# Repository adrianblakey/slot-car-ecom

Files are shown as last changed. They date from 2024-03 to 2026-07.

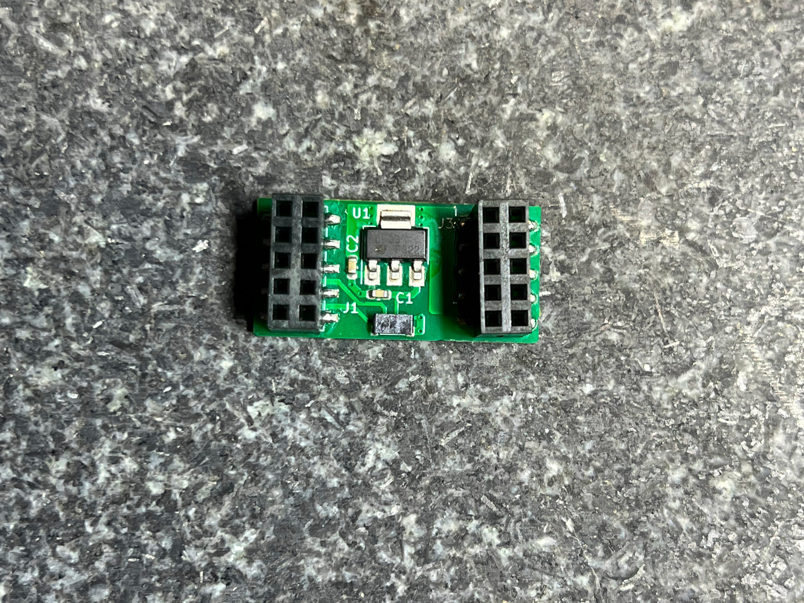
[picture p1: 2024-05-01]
images/aart-adapter.jpg

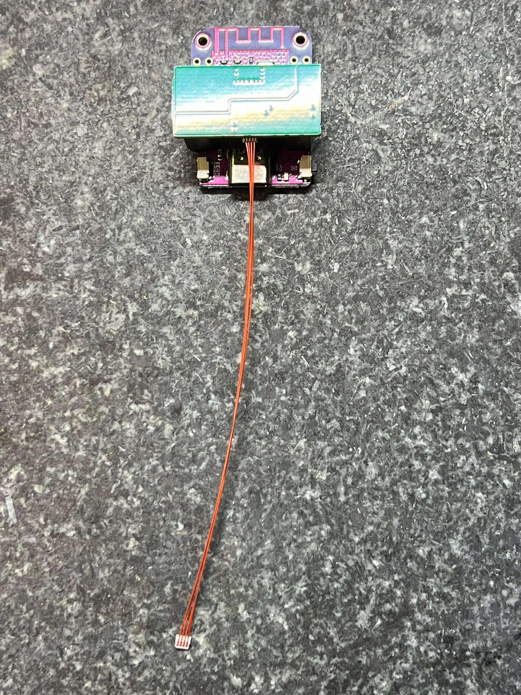
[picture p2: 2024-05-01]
images/wifi-link.jpg

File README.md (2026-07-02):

# The Remora&trade; 1 - Slot Car eCom

This repo contains a [KiCad](https://www.kicad.org/) design, documentation and ancillary artifacts for a slot car brushless motor electronic commutator or "eCom", also known as an Electronic Speed Controller (ESC).

If you are looking for our latest board - the Remora&trade; 2 - you find it here: https://github.com/aartech-dev/Remora2 Please note this is in a different github organization to where we'll eventually move this repo.

All the intellectual property herein is released under a modified [creative commons license](https://github.com/adrianblakey/slot-car-ecom/blob/main/AART_Remora_eCom_License_v1.2.pdf). Under the terms of this license you are free to use everything you find here and make your own eCom from the distributed files as long as you comply with certain rules that are spelled out in the above document. We hope that by doing so we'll stimulate innovation and experimentation. If you have suggestions for improvement please file a bug report and tell us about it. 

There is a [remora1 discussion channel on Discord](https://discord.gg/e3FdfGwk2X) to provide feedback. Also, a good place to get help is the [ESCape32 slot car discord channel](https://discord.gg/XNwYPM7E). ESCape32 is the firmware we have used to run this eCom it's also open source and you'll find it on [github too.](https://github.com/neoxic/ESCape32)

There is nothing stopping you from making your own copies of this eCom. As a hobbyist, or manufacturer everything is here to help you do that. As a hobbyist and with a bit of effort you can make very small quantities at very reasonable cost.

If you choose to manufactuer the parts and sell them as a finished product we ask that you negotiate a small royalty payment with us. These designs are open but not free - all the intellectual property (IP) in this repo. belongs to us. If you have a product you are selling that's based on our IP and it's out there in the marketplace we'll know about it because it's a small (slot car) world. If you are making and selling our designs please talk to us and be up front about it. We incur some real expenses to create this and we want to continue innovating. To do that requires some income and that comes from making parts from the design and selling them.

You should also know that if you are making and selling parts it's your responsibility to support the people who buy them. We are more than happy to help you do that if we are receiving some compensation from you. We've been very generous with the amount of information that we have shared publically on this WiKi to make support simpler. If you choose to republish this information you are under obligation of our [License](https://github.com/adrianblakey/slot-car-ecom/blob/main/AART_Remora_eCom_License_v1.2.pdf) to acknowledge its source. 

We also ask that nothing here is used for military purposes. This also applies to the ESCape32 firmware.

Please refer to the [WiKi for detailed information](https://github.com/adrianblakey/slot-car-ecom/wiki).

Communicate with us on the slot-car channel of the [ESCape32 Discord server.](https://discord.gg/b9SHzh3eSR)

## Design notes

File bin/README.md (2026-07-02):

This repo contains experimental binaries - USE AT YOUR OWN RISK.

We know that high Kv motors are easier to commutate using higher pwm frequencies. The off-the-shelf ESCape32 binaries place restrictions on the values for freq_min/max (16-48, 16-96) - probably because several ESCape32-targetted mcu's run at slower clocks than the F421 and the "market" for this firmware is more conservative drone motors - not outrageous (22,000Kv) slot car motors. 

These binaries expand and raise the pwm limits (24-96, 24-200) to values that are just below the possible theoretical values supported by the Artery F421 peripherals. The freq_min limit is more critical that the freq_max limit. Also, the 2:1 ratio in the ESCape32 firmware is removed allowing you to pick values yourself.

Also know that pwm is used only during the start and synchronization of a motor, and not once it's running when pwm is turned off and effectively running at 100% duty cycle.

If you are curious to see the changes, they are in a fork of the EScape32 repo in my own repo e.g. https://github.com/adrianblakey/ESCape32/blob/master/src/util.c#L435

And eh, yes the fixes were Vibe-coded using claude.ai - so use at your own risk and report bugs :-)

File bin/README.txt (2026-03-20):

Binaries that implement an ability to set pwm_min to a freq upto a not so sensible 96kHz and pwm_max to 200

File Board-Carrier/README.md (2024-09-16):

A little gift - the CAD file to 3D-print a board carrier,

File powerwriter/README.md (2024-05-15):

This pkg file configures the PowerWriter, Windows flashing software. Use the first tab in PowerWriter and hit "open", 
then navigate to where you have this file on the Windows machine in th dialog, and use the password "remora1" to access it.

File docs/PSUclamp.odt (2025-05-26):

PSU Clamp Test Waveforms & Calculations

April & May 2025

# Setup

Motor: EMAX ECO 1106, Kv = 6000, 12 magnets, with flywheel

Connections: Separate connection from power supply to Remora & from power supply to the clamp circuit

Clamp Circuit Schematic | Q1: the prototype used SQJ140ELP mounted on a copper sheet 15mm × 8mm × 0.5mm A few other possible mosfet candidates: Part Number Package SQJ140ELP PowerPAK (5x6) SQJ160EP PowerPAK (5x6) IRFS7437 D²PAK SQM40016EM D²PAK 7 lead RFP50N06 TO-220 SUP50020EL TO-220 IRLB3034 TO-220 Q2: the prototype used KSA733, but almost any small PNP transistor would work.

# Method

In the ESC32 menu move slider right then left, this rapidly stops the motor sending energy back to the power supply (PSU), as power supplies only source current this raises the PSU voltage.

The clamp is designed to start operating at about 12.5V preventing damage to the WiFi and Remora.

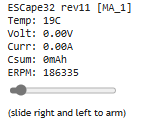
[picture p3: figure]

ERPM = rpm × pole pairs ∴ rpm = ERPM ÷ pole pairs ∴ rpm = 186335 ÷ 6 = 31056rpm

From Kv value: rpm ≈ 5V × 6000Kv = 30000rpm, so in reasonable agreement with ERPM reading from ESC32.

Commutation frequency, Fc = (rpm / 60) × pole pairs = ERPM / 60 = 186335/60 = 3106Hz

Measured Fc from oscilloscope is 3003Hz

Supply rail voltages & mosfet gate voltage

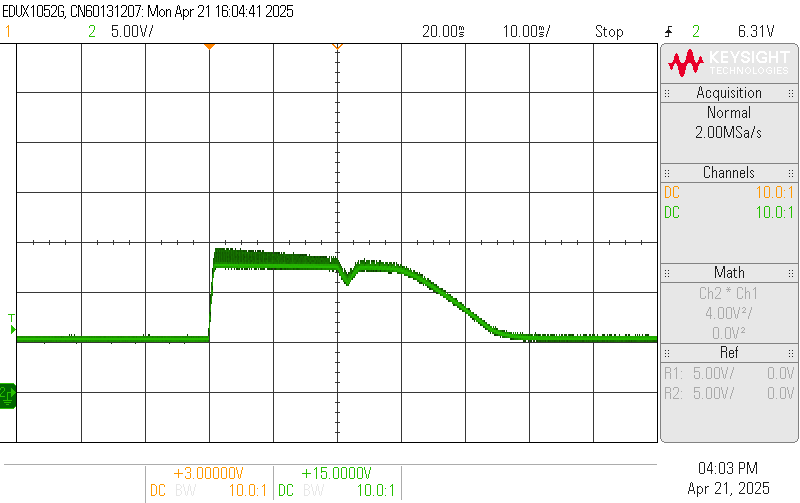
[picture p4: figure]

| 1 5V supply green = supply at Remora, 5V/div, 10ms/div Supply starts at 5V, then when the slider is moved left it rapidly rises to the clamp level of about 12.5V. The clamp successfully holds the voltage at below 15V.

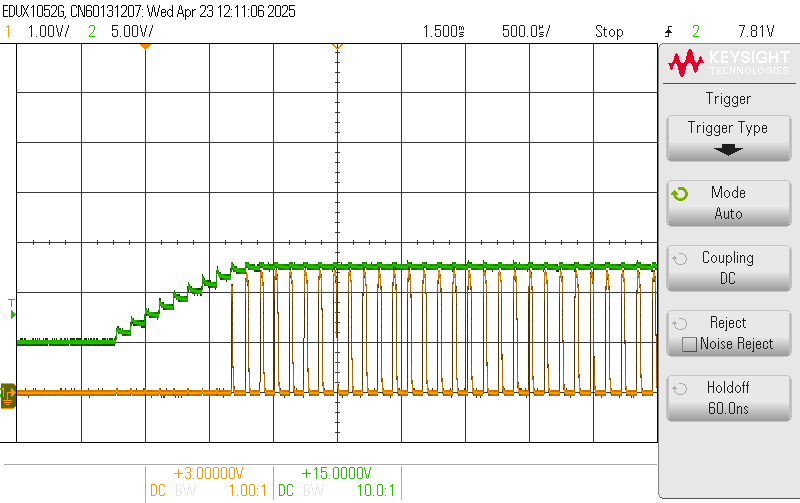
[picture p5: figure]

| 2 5V supply yellow = mosfet gate, 1V/div, 500µs/div green = supply at clamp, 5V/div, 500µs/div The pulses occur at 3× the commutation frequency. Initially at ≈115µs period ≈ 9kHz Therefore one pulse for each of the ecom 3 phases. See waveform 4 for an individual phase.

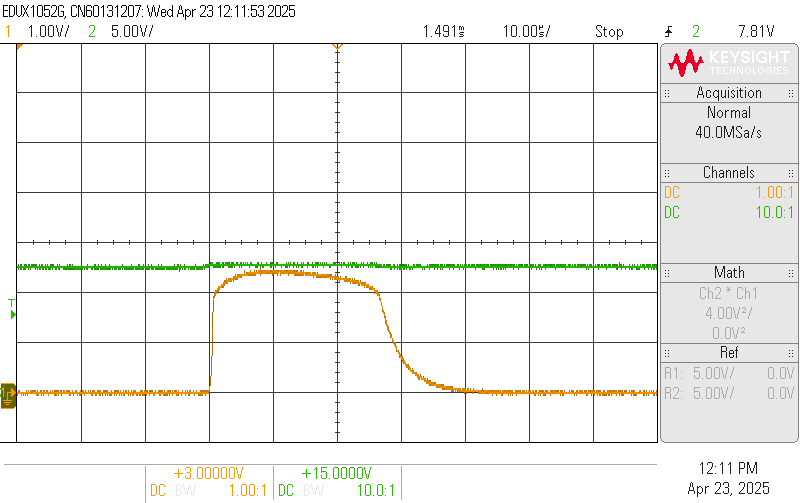
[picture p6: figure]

| 3, zoom of 2 5V supply yellow = mosfet gate, 1V/div, 10µs/div green = supply at clamp, 5V/div, 10µs/div Gate voltage returning to zero indicates that the mosfet is being turned on & off during the clamping phase. The voltage remaining high must then be due to the capacitance in the PSU & Remora.

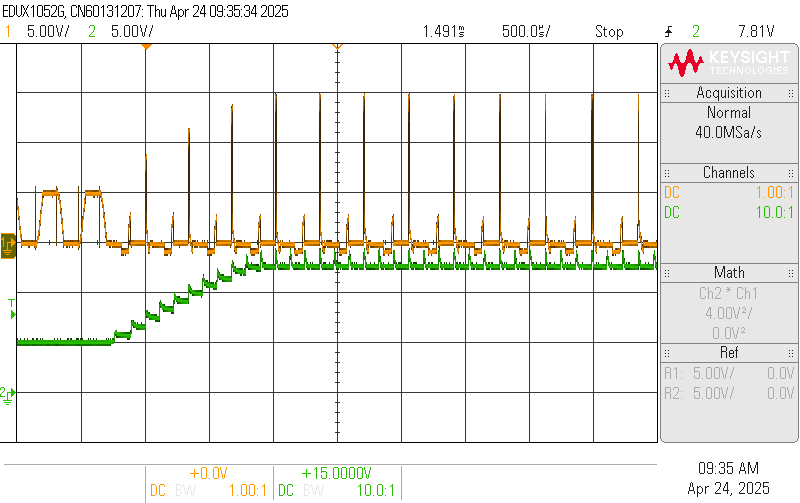
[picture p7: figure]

| 4 5V supply yellow = ecom V phase output, 5V/div, 500µs/div green = supply at Remora, 5V/div, 500µs/div The high amplitude (>10V) spikes on V-phase occur at the commutation frequency.
currents (Remora settings slightly different to those for voltage measurements above, running at slightly higher rpm)

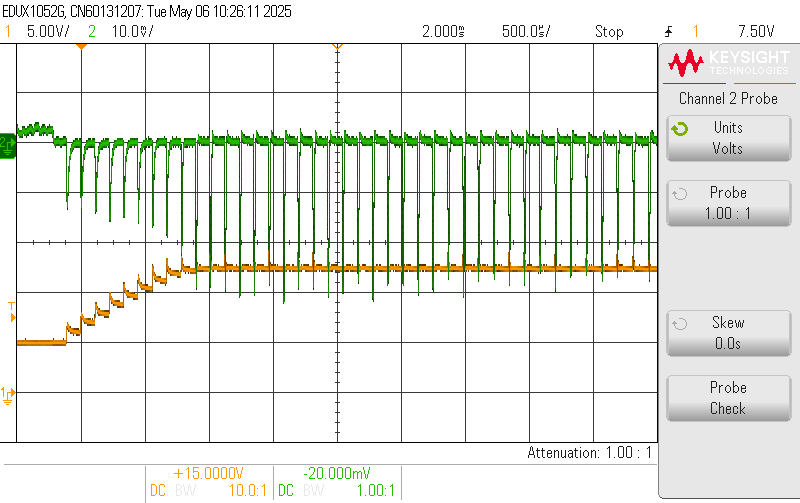
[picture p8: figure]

| 5 5V supply yellow = supply at Remora, 5V/div, 500µs/div green = current in Remora +ve line, 2A/div, 500µs/div The spikes occur at 3× the commutation frequency, i.e. one for each phase. Initially at ~ 110µs period

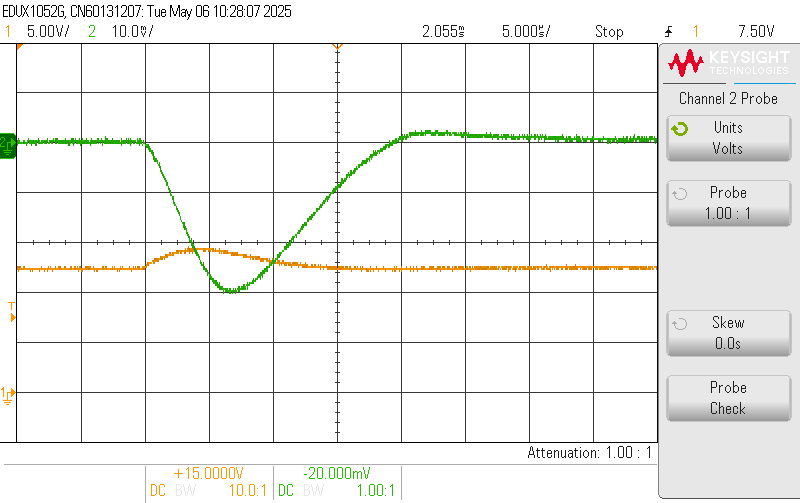
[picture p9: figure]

| 6 zoom of 5 5V supply yellow = supply at Remora, 5V/div, 5µs/div green = current in Remora +ve line, 2A/div, 5µs/div 6A peak current fed from Remora to PSU & clamp circuit. Approximately a triangular shape width 20µs So average current ≈ 6A ÷2 × 40µs ÷ 110µs = 1.1A The current & voltage both start to rise at the same time, but peak current is lags the peak PSU voltage by about 6.8µs

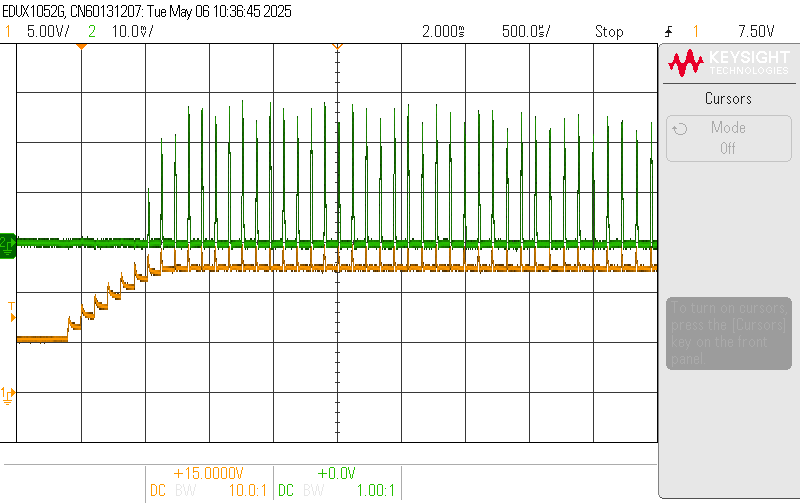
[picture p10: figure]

| 7 5V supply yellow = supply at Remora, 5V/div, 500µs/div green = current in clamp +ve line, 2A/div, 500µs/div

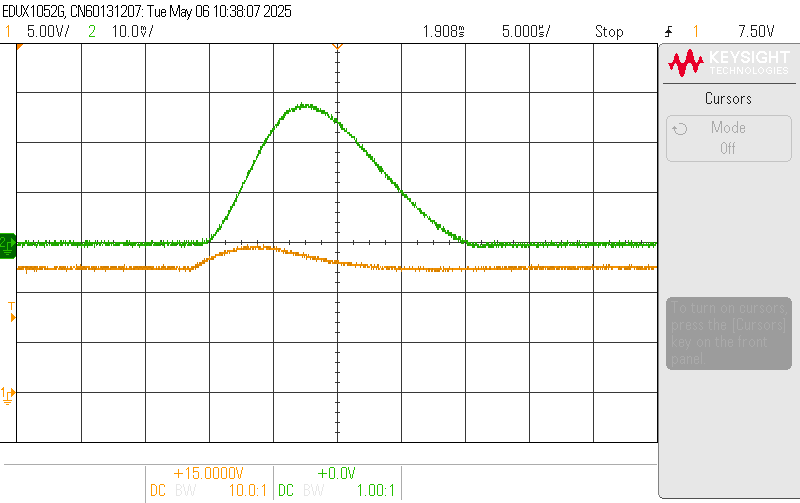
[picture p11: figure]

| 8 zoom of 7 5V supply yellow = supply at Remora, 5V/div, 10µs/div green = current in clamp +ve line, 2A/div, 10µs/div peak current & width are very similar to the current from Remora, but some current must be flowing into the power supply output capacitor as indicated by the rise in the voltage. The rise in current is delayed from the start of the voltage rise & the peak current lags the peak PSU voltage by about 9µs

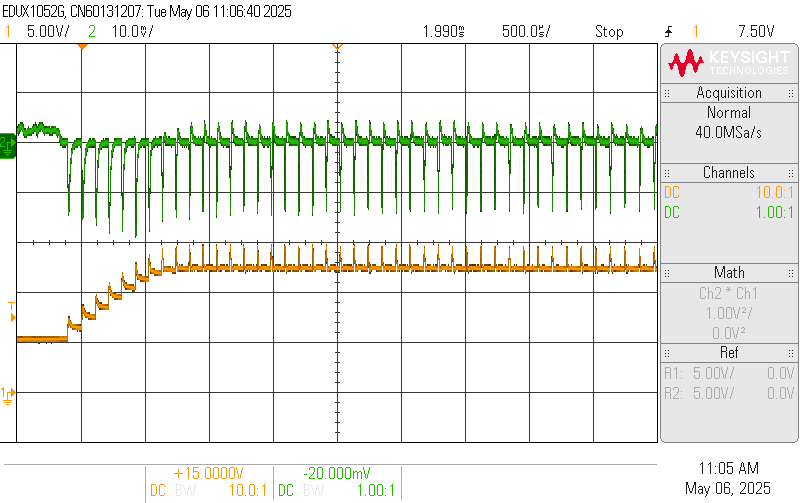
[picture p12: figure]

| 9 5V supply yellow = supply at Remora, 5V/div, 500µs/div green = current in PSU +ve line, 2A/div, 500µs/div

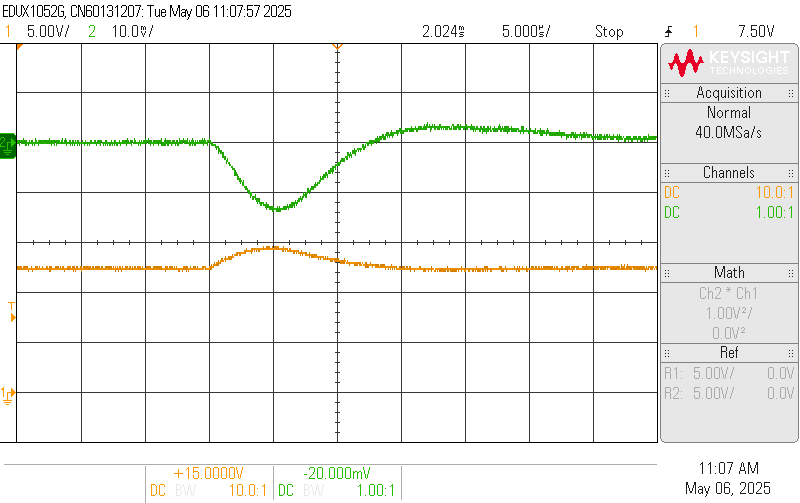
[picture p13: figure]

| 10 zoom of 9 5V supply yellow = supply at Remora, 5V/div, 5µs/div green = current in PSU +ve line, 2A/div, 5µs/div The current & voltage both start to rise at the same time, and peak current is coincident with the peak PSU voltage

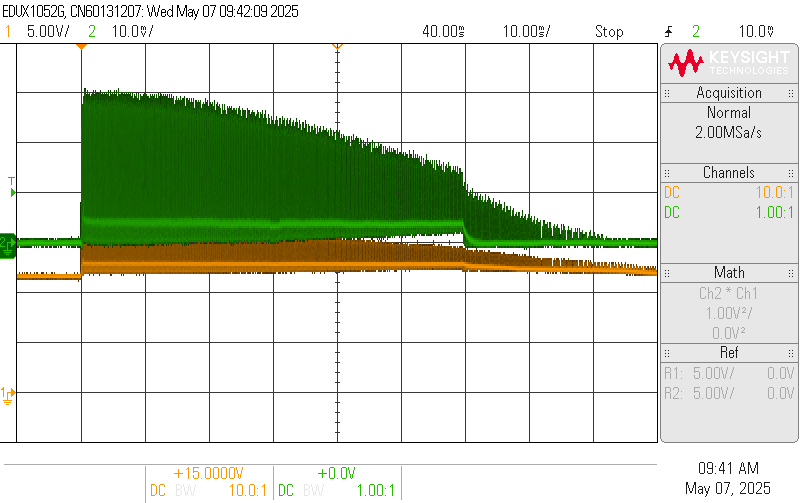
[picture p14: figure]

| 11 11.5V supply yellow = supply at Remora, 5V/div, 10ms/div green = current in clamp +ve line, 5A/div, 10ms/div

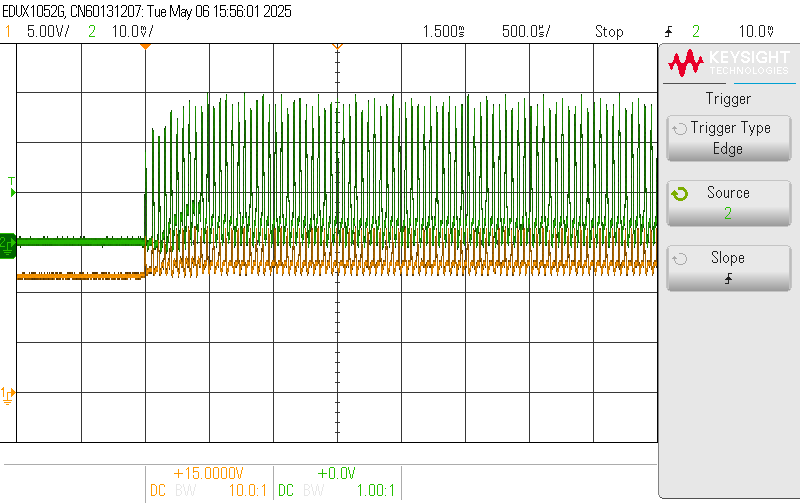
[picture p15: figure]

| 12, as 11 but faster time-base 11.5V supply yellow = supply at Remora, 5V/div, 500µs/div green = current in clamp +ve line, 5A/div, 500µs/div

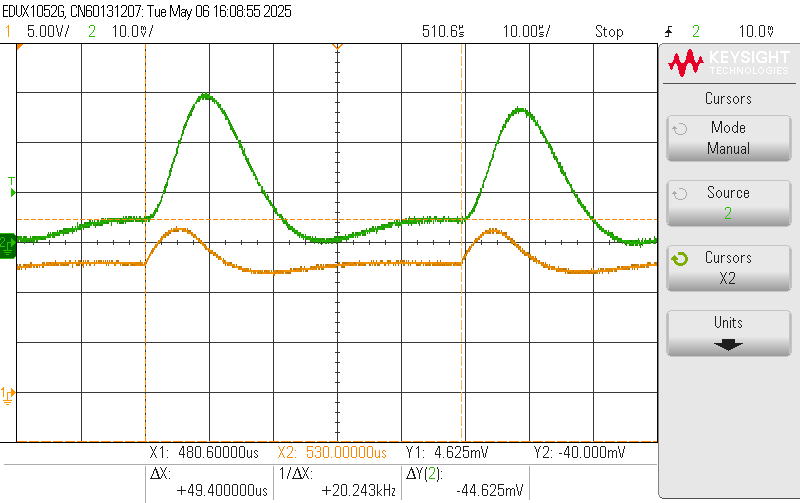
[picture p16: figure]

| 13 zoom of 12 11.5V supply yellow = supply at Remora, 5V/div, 10µs/div green = current in clamp +ve line, 5A/div, 10µs/div ipk = 14.5A iav from scope measurement =4.22A irms from scope measurement = 6.1A current prior to steep rise = 2.3A period = 49.4µs Approximately a triangular shape width = 23µs 2.3A step width = 9.4µs 0A to 2.3A ramp width = 10µs check on iav: Iav ≈ [(14.5÷2×23µs)+ (2.3÷2×10µs) + (2.3×9.4µs)]÷ 49.4µs = 4A, in reasonable agreement with scope measurement. Vpk = 16.5V Vav = 13.25V so power = 13.25V × 4.22A = 56W scope maths = 55W From waveform 11 duration ≈ 60ms so energy 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
Mosfet Safe Operating Area (SOA) & Thermal considerations

Mosfet SOA

Using IRLB3034 as an example of an SOA chart, because used it in the thermal calculation example below

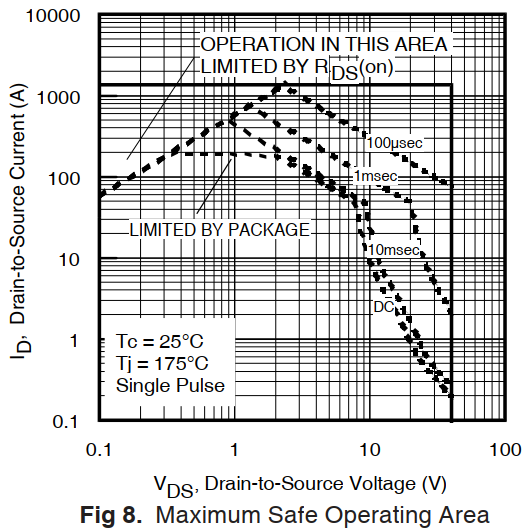
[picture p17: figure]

At 11.5V supply the current pulses are about 15A with a triangular shape of width 23µs, but to allow a generous safety margin use 30A & 50µs. SOA data usually has plots of curves at 100µs so use this instead of 50µs giving an even greater safety margin. The voltage for the SOA will be 15V.

Taking the IRLB3034 SOA as an example its DC SOA at 15V is only about 3A, but its 100µs SOA is about 200A, however this is for a temperature rise of 150°C from 25°C to 175°C. For a good lifetime better to restrict the temperature rise to 75°C so therefore the 100µs SOA current would be reduced to 100A.

This is still in excess of our requirement of 30A so is OK.

The actual temperature rise for the 15A 23µs triangular pulse will be very considerably lower than 75°C.
Thermal calculations just to get an estimate of whether a heatsink is required or not. | thermal energy formula: Q = m × c × Δt Q = energy J m = mass kg c = specific heat capacity J / kg · K Δt = temperature rise K (or °C) If the energy was dumped in an aluminium heatsink specific heat capacity = 900 J / kg · K allow 20K temperature rise for the aluminium ∴ mass = 0.19g If the energy was dumped in a copper sheet specific heat capacity = 385 J / kg · K allow 20K temperature rise for the copper sheet ∴ mass = 0.44g For reference the total mass of a TO-220 is about 1.9g, so it may be able to absorb the energy without an additional heatsink.
Thermal simulation model Using IRLB3034 in a TO-220 package as an example. Because it has a thermal model on the data-sheet. (Although it only has a moderate DC SOA its pulse SOA is acceptable). Triangular power pulses applied with 55W average, see waveform 13. R5 with a thermal resistance of 62K/W represents a TO-220 without a heatsink. In the model: current represents thermal power voltage represents temperature | IRLB3034 thermal model results Red = junction temperature rise at 60ms, average = 50°C & temperature ripple due to the individual triangular power pulse is small at about 2°C. green = TO-220 case temperature rise, at 60ms = 35°C So a TO-220 package without a heatsink has an acceptable temperature rise for a single 60ms burst of pulses, even with an 11.5V supply.

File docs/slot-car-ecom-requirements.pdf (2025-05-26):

Sheet1
Priority | Name | Description
High

High

High

High

High

| Startup

High

| | Shall be able to run without pwm once the motor is synchronized and started.
High | Maximum rpm

High

High | Motors | Shall be able to drive very low inductance and resistance motors.
High | Motor range
High | Algorithm | Shall be able to run a 6-step algorithm.
High | Size
Medium | Weight | Shall weigh less than 2.5gm
High | Power up time
| Startup
High | | Shall preferably use the same STM32G071 mcu as some of the competitor eCom
Low | Mcu shall have a way to sense the supply voltage.

Reverse
polarity
protection

Shall be protected from reverse polarity. It shall only be possible to power the ESC with plus and minus connected to their designated pads on the board.
Reverse
polarity
protection
response

Shall provide reverse polarity protection in less than 2 ms, (the time it might take for a car to end up in a lane facing the wrong direction)

Startup/
shutdown
voltage

Shall start at less than 1.2V and stay energized when running down to 1.18V.

Typical
voltages

Shall be able to operate efficiently in the range 10 Vdc to 12.6 Vdc – typical maximum track supply voltages for recreational play to competitive racing. Maximum
voltage

Shall be able to run with track supply voltages up to 16.4V and survive at 18V for short periods of time
Shall control the power to the motor using pulse width modulation (pwm), with aspects of the rate and size of power provided to the motor set by firmware parameters.
Linear
operation

Shall be able to act linearly over its range of voltages so that say if the minimum activation voltage is 1.2V and the maximum track voltage is 12.4V the esc shall deliver 1.2V to 12.4V to the motor.
Normal
operation
Shall be capable to commutating 6 magnet motors up to ~270,000 rpm and 12 magnet motors up to ~180,000 rpm.

Thermal
performance

For compatibility with similar products specifically designed for slot-car use the sum of the maximum on-state resistances of the reverse polarity mosfet + the high-side mosfet + the low-side mosfet shall be ≤ 13mΩ

Shall be able to run 1102/3/4/5/6/8 and 1203/4 motors in a range of Kv from say 2,000Kv – 22,000Kv

Shall be physically close to similar slot-car eCom size and be no larger than 25mm × 16mm × 4.5 – 5mm

The time from application of 12V to the input supply terminals to the motor outputs starting to switch shall preferably be less than 2ms, but not more than 4ms.
The startup synchronization phase should allow for PWM at 24kHz or 48kHz or 96kHz for about 100ms.
Microcontrolle
r choice

Supply voltage
sensing

High | Tunability
High | Debug | Shall be possible to attach a debugger to the part (SWD pins)
High | Write | Shall be possible to write (flash) new firmware to the part.
High | Updates
High | | Shall be possible to backup or read firmware from the part once it’s flashed.
High | Parts supply
High | Parts cost
Medium | Layout
High | Labeling
Medium | Part choice

High

Medium | Layout | Double side component mounting is allowed

Shall be able to fine tune the the ESC to achieve maximum motor performance and efficiency, either by feedback from the motor itself or direct input to the ESC.

Shall be possible to modify the firmware operating parameters and have them saved persistently.
Read
protection
Shall be designed to use parts that are commonly available from JLBPCB or PCBWAY (or another contract assembler) so we can manufacture it.
The parts cost shall not constrain the choice of parts, i.e. choose the best parts to implement the design constraints.

The final parts shall be laid out conventionally with two input voltage pads on the top layer, the right front being positive (to the wire to the right front guide input), and three motor connection pads at the top on the top layer rear.

The part shall have sufficient silk screen labeling to identify the pins to remove installer confusion.
If possible the variety of parts shall be minimized, but not to the detriment of the implementation.
Under voltage
lockout

Any Under-voltage lockout features should not cause either all high-side or all low-side mosfets to be in the on-state, to prevent a short circuit being applied to the motor.

comments

See the ESCape32 configuration parameters.

See the ESCape32 configuration parameters.

Height is set in a range to account for different manufacturing possibilities and copper weights.

May be possible to specify an overall board thickness <1.6mm, to save weight, but may cost more All power rails start quickly enough

See the ESCape32 configuration parameters.

With pwm turned off (parameters duty_min and duty_max set to 100) then the output voltage will be the same as the input voltage less some small losses.
For the speed controller to commutate a motor at high rpm it has to be able to commutate at a proportionally higher frequency.
The commutation frequency Fc = (rpm / 60) * pole-pairs
Typical slot car motors have either 6 or 3 pole pairs (12 magnets or 6 magnets). The fastest motors running at up to 22,000Kv are 6 magnet motors.
For 6 pole pairs at 150000rpm ; Fc = (150000/60)*6,~ 15kHz
And similarly - 3 pole pairs at 270000rpm; Fc = (270000/60)*3,~ 13kHz
Note: Some competitor eCom’s start to have problems at 10kHz.
A No-load 180,000rpm nominally represents a 10,000Kv motor running on 18V
Or a 3,800Kv at 39.5V Let's say it's 180k RPM max.
With a 12 magnet motor, it's 180000*12/2=1080 kERPM.
1080000/60=18000 commutations per second, or one commutation every ~56µs (microsecond) All N-ch mosfet output stage, with maximum on-state resistance of 4.2 mΩ each, therefore allowing 4.6mΩ for the reverse polarity mosfet
2µH to 20µH
30mΩ to 300mΩ
Tested a 1207.

In order to drive a 18000Kv motor this requirement can not be met with a 64MHz mcu. The G071 MCU running at 64Mhz can get around 750*1.33=1M erpm, (RPM = ERPM/ pole pairs) With 12pole it’s 1000000/6=166kRPM. For ~1.2M ERPM (or 200kRPM), a faster MCU is needed. The AT32F421 is one of the candidates (however it has some startup delay). Better still would be STM32G43.
The AT32F421 is almost twice as fast as the G071. The STM32G431 is even faster than that running at 170Mhz.

All parts have JLCPB reference number.

Fortior gate drive IC is OK

Brushed DC slot-car motors have commutator advance, to improve their performance in one direction of rotation, it may well be that the brushless motors would also benefit from advance built into the firmware. This is a feature of the Escape32 firmware. Access via 4-way connector to allow access to mcu pins
Need to specify where the pads can be located, their size & spacing, without going to any extra expense the pads can go down to 1mm diameter and connect to them using small pogo test pins in an accurately constructed programming jig.
The pads could go down to 1.27mm pitch, 2.54mm would be more “comfortable.”

The hardware design process usually involves close scrutiny of part cost vs performance. Its relatively easy to get the performance you want if cost is no constraint, but its also possible to get the same performance at lower cost if time is taken to carefully choose the components & the design itself. And surely the final selling price is an important parameter.
Pad size: The target is about 3×3.5mm but it could easily be smaller if need to save space. Hawk motor terminals are 2mm wide and the useful length is about 3mm, people are quite used to soldering to relatively small terminals say 2.5x2.5mm (0.1”x0.1”) as a minimum. See diagram showing the preferred position of the pads. Layout time constraints resulted in Remora1 input pads being reversed. Output pads allow for a 2mm pitch right-angle pin header.
Labels shall be: +, -, U, V, W, (swd)C(om), (swd)I(o)
Note: If there’s space labels could be in the copper layer to save having silk screen.

+ -

m

m

m

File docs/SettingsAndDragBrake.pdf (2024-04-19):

duty min max

## hand-controller , track settings

DATA | value | units
anti-brake voltage | 1.2 V
hand-controller sensitivity (min voltage) | 2.5 V
track supply voltage (max voltage) | 12 V

CALCULATION
m 0.3064516129
c 2.1935483871
assuming output voltage is linear with respect to wiper position, not quite correct but good enough to demonstrate the effect of the settings

Remora duty %

0 | 1.2 | 0 | 0 if Remora duty is 0, drag brake can be active
1 | 2.5 | 0 | 0 set by duty_drag
2 2.8064516129 | 0 | 0
3 3.11290322581 60.6451612903 1.8878251821
4 3.41935483871 62.3963133641 2.13355136019
5 3.72580645161 64.1474654378 2.39001040583 6 4.03225806452 65.8986175115 2.65720231901 7 4.33870967742 67.6497695853 2.93512709975 8 4.64516129032 69.400921659 3.22378474803 9 4.95161290323 71.1520737327 3.52317526386 10 5.25806451613 72.9032258065 3.83329864724 11 5.56451612903 74.6543778802 4.15415489817 12 5.87096774194 76.4055299539 4.48574401665 13 6.17741935484 78.1566820276 4.82806600268 14 6.48387096774 79.9078341014 5.18112085625 15 6.79032258065 81.6589861751 5.54490857737 16 7.09677419355 83.4101382488 5.91942916605 17 7.40322580645 85.1612903226 6.30468262227 18 7.70967741935 86.9124423963 6.70066894604 19 8.01612903226 88.66359447 7.10738813736 20 8.32258064516 90.4147465438 7.52484019622 21 8.62903225806 92.1658986175 7.95302512264 22 8.93548387097 93.9170506912 8.3919429166 23 9.24193548387 95.668202765 8.84159357812 24 9.54838709677 97.4193548387 9.30197710718 25 9.85483870968 99.1705069124 9.77309350379
26 10.1612903226 | 100 10.1612903226
27 10.4677419355 | 100 10.4677419355
28 10.7741935484 | 100 10.7741935484
29 11.0806451613 | 100 11.0806451613
30 11.3870967742 | 100 11.3870967742

hand-controller
wiper position

hand-controller
output voltage

effective
voltage to
motor

2

4

6

8

10

12

14

voltage

0

## firmware settings

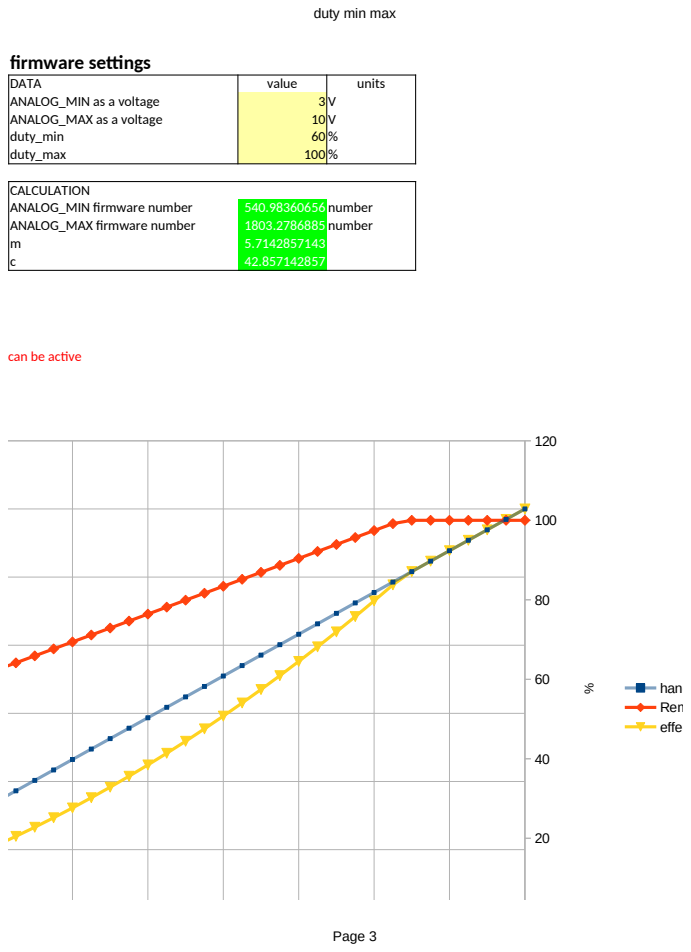
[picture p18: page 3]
DATA; value; units; ANALOG_MIN as a voltage; ANALOG_MAX as a voltage; duty_min; duty_max; CALCULATION; ANALOG_MIN firmware number; 540.98360656 number; ANALOG_MAX firmware number; 1803.2786885 number

hand-controller output voltage
Remora duty %
effective voltage to motor

hand-controller output voltage Remora duty %
effective voltage to motor

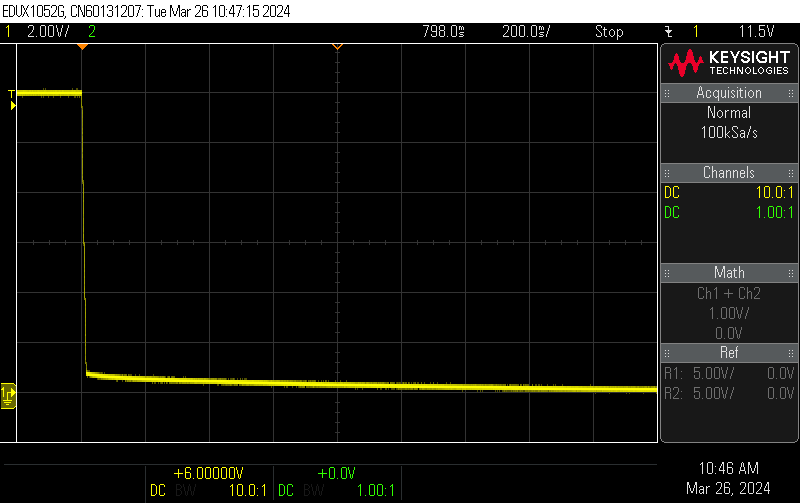
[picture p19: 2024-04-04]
images/braking1.png

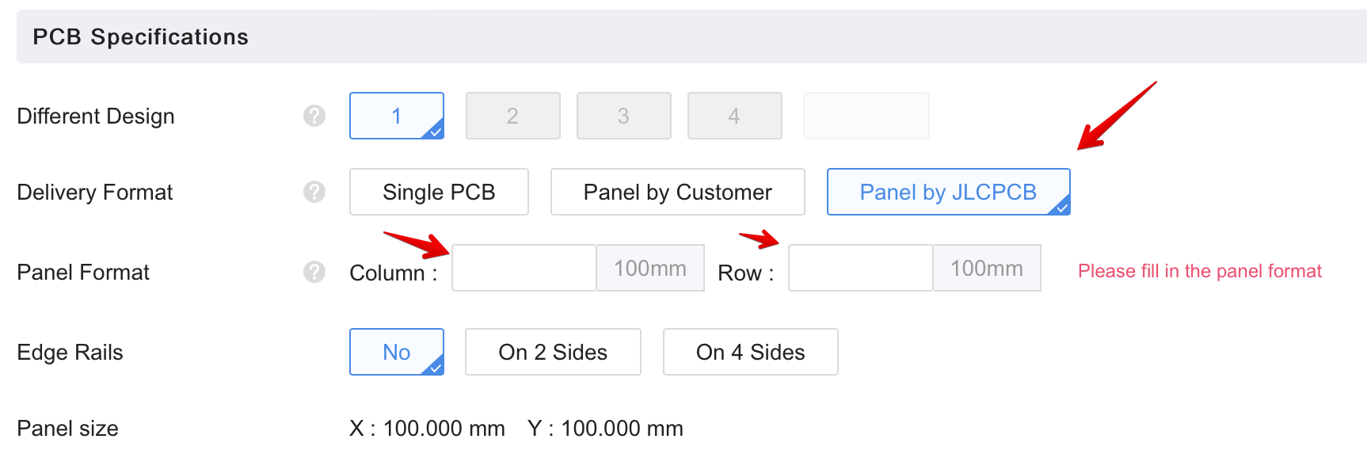
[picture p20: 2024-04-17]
images/panelize_jlcpcb.png

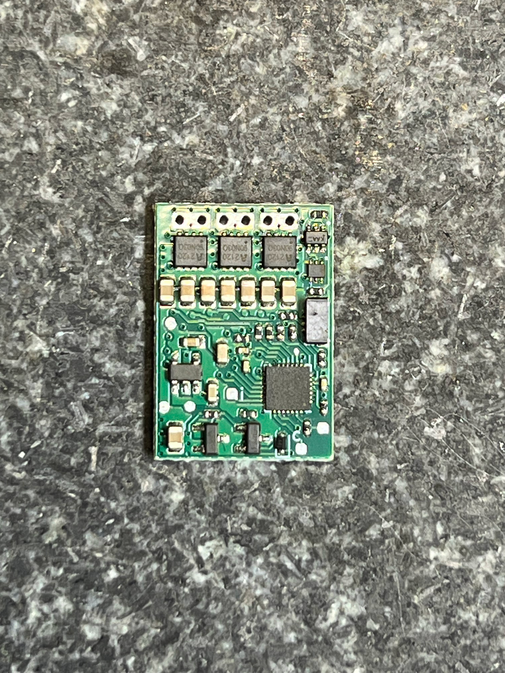
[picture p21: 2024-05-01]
images/remora1-top1.jpg

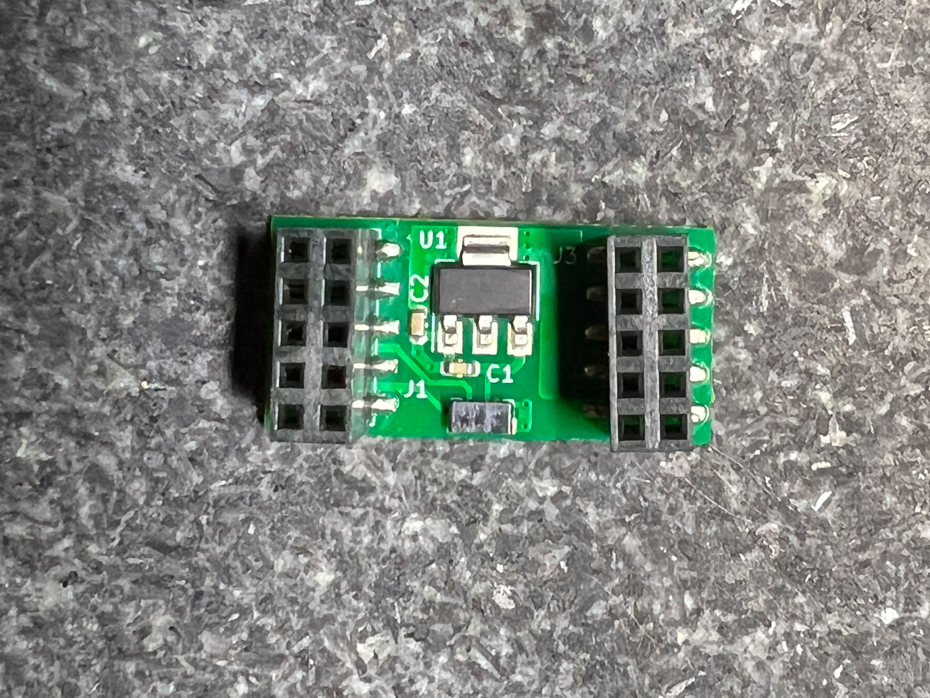
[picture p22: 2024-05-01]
images/aart-adapter1.jpg

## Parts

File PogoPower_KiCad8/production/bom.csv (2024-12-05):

Designator | Footprint | Quantity | Value | LCSC Part #
J1, J2, J3, J4, J5 | PogoRecptacle_D1.4mm_OD2.0mm | 5 | Conn_01x01
J8 | PinHeader_2x04_P2.54mm_Vertical | 1 | Conn_02x04_Odd_Even

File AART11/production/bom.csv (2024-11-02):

Comment | Designator | Footprint | JLCPCB Part #
TestPoint | +, GND1 | TestPoint_Pad_2.5x2.5mm
100nF | C1, C22, C23 | 402 | C1525
1uF | C10, C3, C5 | 603 | C15849
22uF | C11, C12, C13, C14, C15, C16, C17, C18, C19, C20 | 805 | C45783
10pF | C2 | 402 | C32949
10uF | C21 | 603 | C96446
2.2uF | C4, C6 | 603 | C23630
220nF | C7, C8, C9 | 603 | C21120
BZX584C8V2 | D1 | D_SOD-523 | C2991969
MMBD4448HTW | D2 | SOT-363_SC-70-6 | C435910
PMEG3030EP | D3 | D_SOD-128 | C255587
RB521SM-40T2R | D4, D5, D6, D7 | D_SOD-523 | C253516
Conn_01x01_Pin | J1 | Pad0.5
Conn_01x01_Pin | J10, J11, J2, J3, J8, J9 | SolderWire-0.15sqmm_1x01_D0.5mm_OD1.5mm
Conn_01x04 | J4 | HDG 1x04 P0.6 Horizontal | C3008763
Conn_01x01 | J5, J6, J7 | TestPoint_Pad_1.0x1.0mm
10uH | L1 | L_Sunltech_SLW2010P | C207862
FMMT718 | Q1 | SOT-23 | C2910189
JMSL0302AU | Q10, Q5, Q6, Q7, Q8, Q9 | VSON-8_3.3x3.3mm_P0.65mm_NexFET | C2890409
EMZ1T2R | Q2 | SOT-563 | C510332
MMBFJ309 | Q3 | SOT-23 | C58012
JMSL0302AU | Q4 | VSON-8_3.3x3.3mm_P0.65mm_NexFET | C2890409
10k | R1, R10, R11, R12, R13, R14, R18, R5, R8, R9 | 402 | C25744
2k2 | R15, R16, R17, R2, R6 | 402 | C25879
1k | R19, R20, R21 | 402 | C11702
4k7 | R3 | 402 | C25900
330R | R4 | 402 | C25104
91k | R7 | 402 | C4147
TestPoint_Small | TP1, TP2, TP3 | TestPoint_Pad_D1.0mm
AP3015KTR-G1 | U1 | SOT-23-5 | C151334
AP2210K-3.3TRG1 | U2 | SOT-23-5 | C176959
FD6288Q | U3 | QFN-24-1EP_4x4mm_P0.5mm_EP2.6x2.6mm | C328453
AT32F421G8U7 | U4 | QFN-28-1EP_4x4mm_P0.4mm_EP2.6x2.6mm | C2765098

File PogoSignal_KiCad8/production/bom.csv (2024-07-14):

Designator | Footprint | Quantity | Value | LCSC Part #
J1 | PinHeader_2x04_P2.54mm_Vertical | 1 | Conn_02x04_Odd_Even

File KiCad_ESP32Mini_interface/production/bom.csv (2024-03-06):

Comment | Designator | Footprint | LCSC Part #
1µF 50V | C1, C2 | 603 | C15849
Conn_02x05_Odd_Even | J1, J3 | C843271_PinSocket_2x05_P2.54mm_Vertical_SMD_OddEven | C843271
Conn_01x04 | J2 | HDG 1x04 P0.6 Horizontal | C509242
LDL1117S33R_SOT223 | U1 | SOT-223-3_TabPin2 | C435835

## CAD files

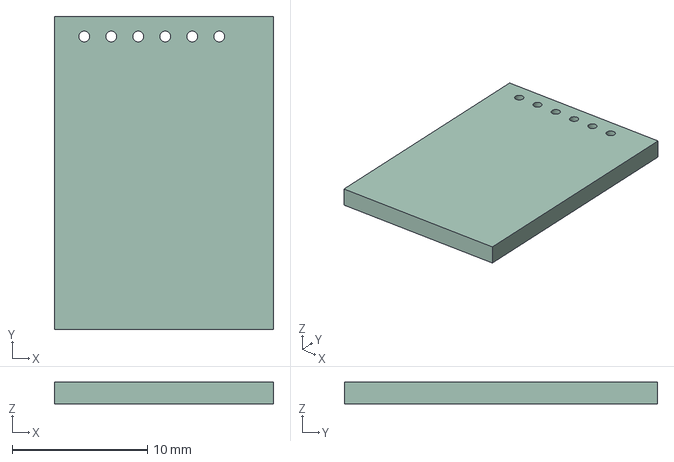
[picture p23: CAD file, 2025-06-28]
AART11/AART11.step
16.2 x 23.2 x 1.60 mm

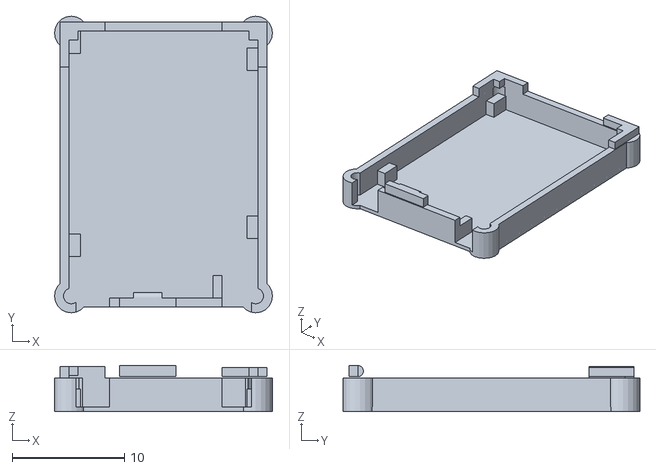
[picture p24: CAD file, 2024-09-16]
Board-Carrier/CradleReverse1.stl
19.4 x 26.4 x 4.10

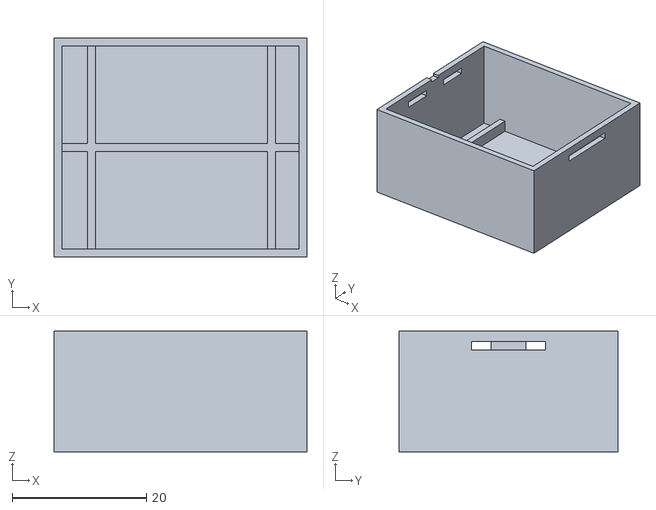
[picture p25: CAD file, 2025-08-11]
WiFi-Link-Encl/WiFiBox2.stl
37.6 x 32.5 x 18.0

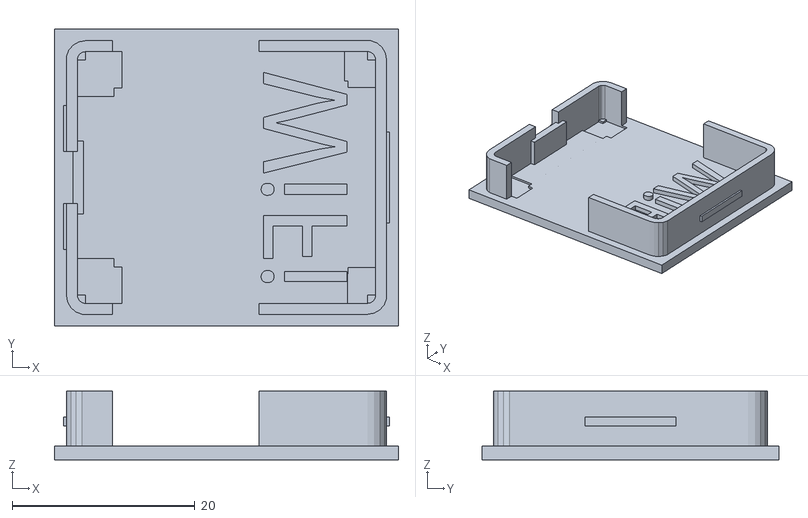
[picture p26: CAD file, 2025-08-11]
WiFi-Link-Encl/WiFi_Lid2.stl
37.6 x 32.5 x 7.50

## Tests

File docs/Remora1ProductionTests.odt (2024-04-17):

Remora1 Production Test

Revision 0.0

December 2023

Pad identification

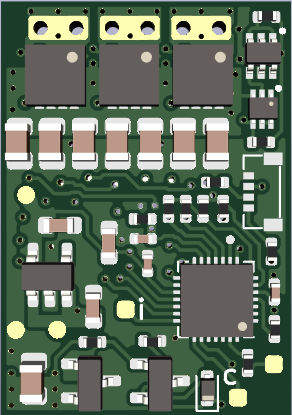
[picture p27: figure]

VCC, 12V4

VDD, 3V3

GND

SWD_IO

SWD_CLK

PB6

VBUS (VIN)

PA2

PA15

GND

VDC,10.3V

Procedure

setup / action | measure | expected result
visual inspection | check for no missing or misplaced parts, no bad joints or solder bridges | all OK
Low Voltage Start & Run
set power supply to 1.5V, but output off
connect power supply to + & - terminals
turn power supply output on | power supply current | 43mA to 52mA
| VCC to GND | 11.954V to 12.914V
| VDD to GND | 3.234V to 3.366V
reduce power supply voltage to 1.25V | power supply current | 75mA to 81mA
| VCC to GND | 9V to 12.914V
High Voltage Test
increase power supply voltage to 13.5V | power supply current | 4.5mA to 7.5mA
| VDC to GND | 8.7V to 12.7V
| VCC to GND | 11.954V to 12.914V
Memory Programming
programme the flash memory
reduce power supply voltage to zero & turn off
Operation With Motor Connected
connect motor, make sure its mechanically secure
turn power supply on
slowly increase power supply voltage | check motor rotation | normal rotation
reduce power supply voltage to zero & turn off
Reverse Polarity Test
reverse connections to + & - terminals
turn power supply on, increase power supply voltage to 13.5V | power supply current | <1.7mA
reduce power supply voltage to zero & turn off
restore normal connections to + & - terminals
turn power supply on, increase power supply voltage to 13V | check for motor rotation | normal rotation
End of Tests
reduce power supply voltage to zero & turn off
end

Revision History

revision | date | changes
0.0 | 29 December 2023 | initial draft, based on 2 prototypes with adaptor board
0.1 | 17 April 2024 | changes based on Remora1 measurements. current at 1.5V revised 1.2V test revised to 1.25V, current revised, VCC to GND revised current at 13.5V revised

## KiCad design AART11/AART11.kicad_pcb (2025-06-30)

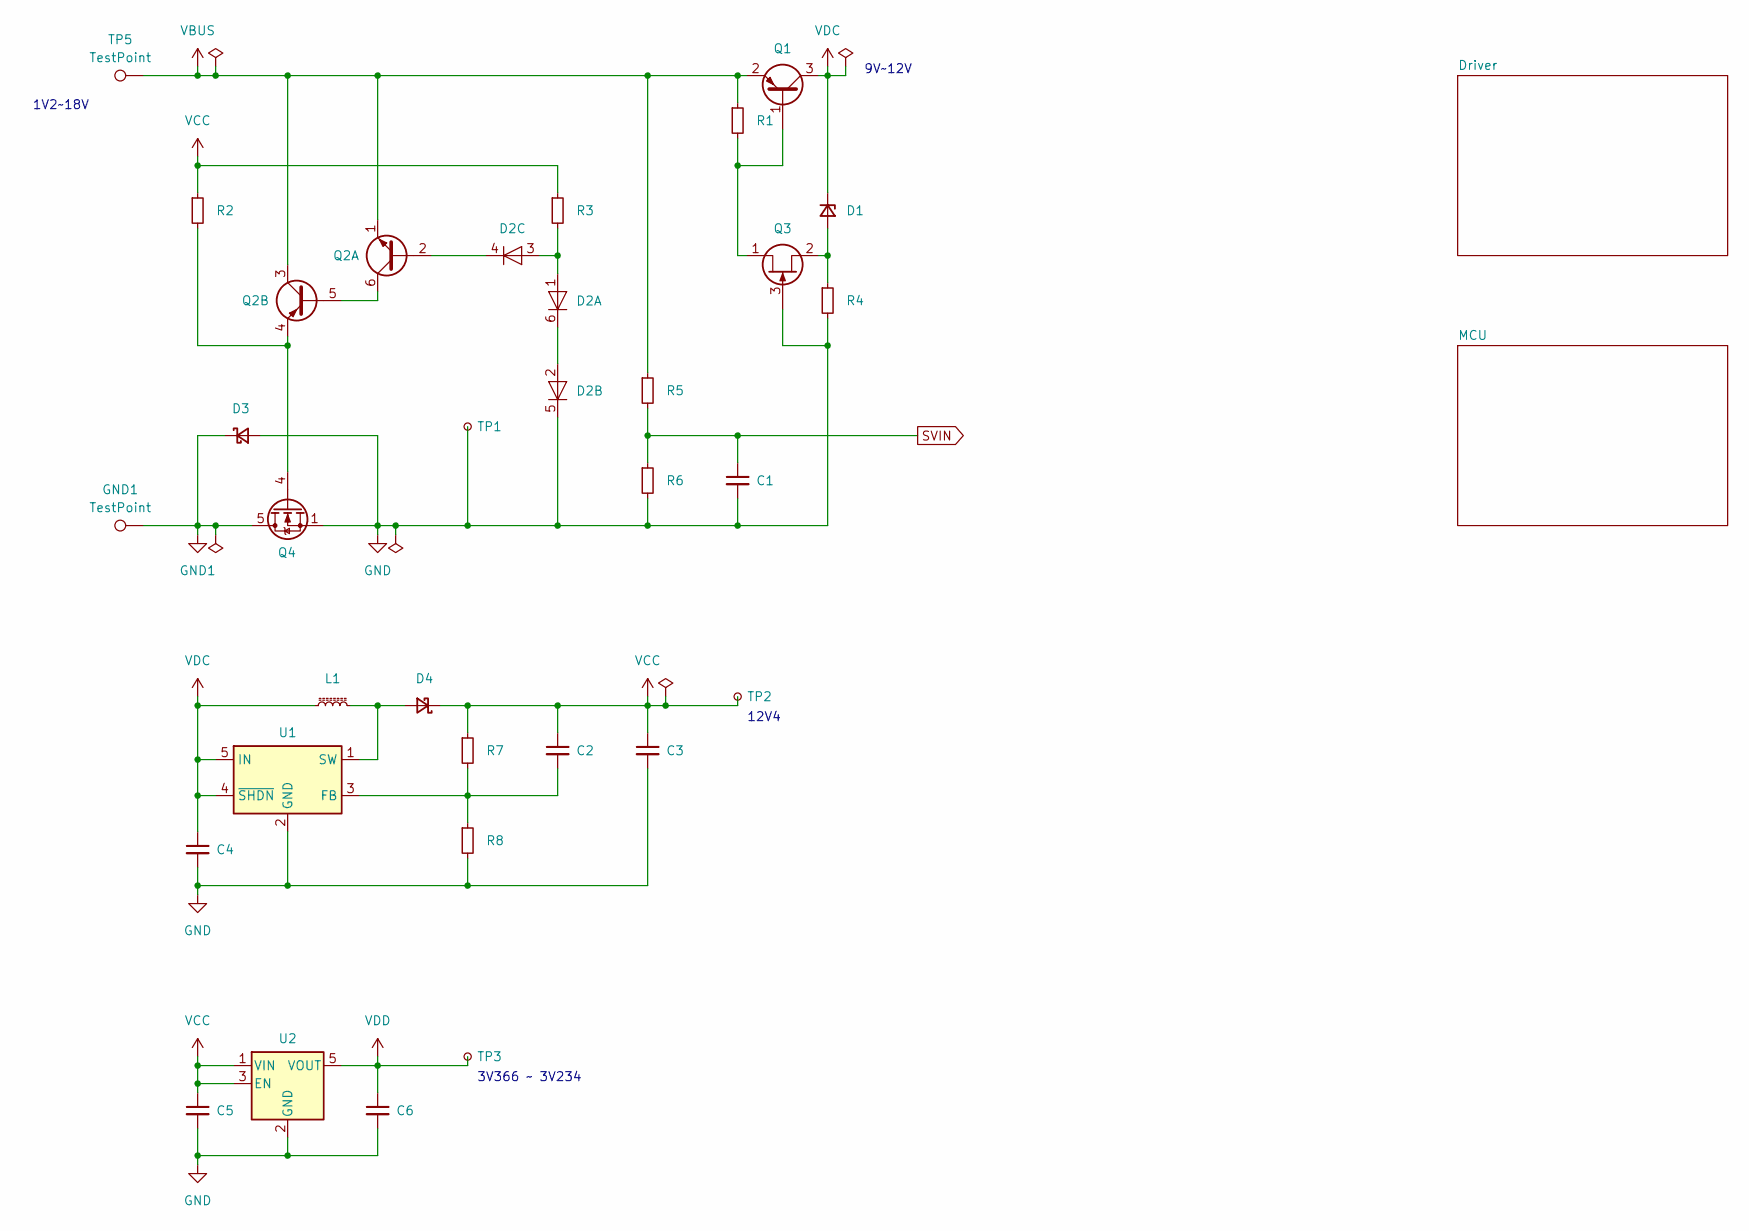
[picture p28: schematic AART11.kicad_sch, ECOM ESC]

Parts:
C1: 100nF; C_0402_1005Metric; Rating X7R - 16V - ±10%; JLCPCB Part # C1525
C2: 10pF; C_0402_1005Metric; Rating C0G - 50V - ±5%; JLCPCB Part # C32949
C3, C5: 1uF; C_0603_1608Metric; Rating X5R - 50V - ±10%; JLCPCB Part # C15849
C4, C6: 2.2uF; C_0603_1608Metric; Rating X5R - 16V - ±10%; JLCPCB Part # C23630
D1: BZX584C8V2; D_SOD-523; JLCPCB Part # C2991969
D2: MMBD4448HTW; SOT-363_SC-70-6; JLCPCB Part # C435910
D3: PMEG3030EP; D_SOD-128; JLCPCB Part # C255587
D4: RB521SM-40T2R; D_SOD-523; JLCPCB Part # C253516
GND1: TestPoint; TestPoint_Pad_2.5x2.5mm
L1: 10uH; L_Sunltech_SLW2010P; Rating 750mA - ±20%; JLCPCB Part # C207862
Q1: FMMT718; SOT-23; JLCPCB Part # C2910189
Q2: EMZ1T2R; SOT-563; JLCPCB Part # C510332
Q3: MMBFJ309; SOT-23; JLCPCB Part # C58012
Q4: JMSL0302AU; VSON-8_3.3x3.3mm_P0.65mm_NexFET; JLCPCB Part # C2890409
R1, R5, R8: 10k; R_0402_1005Metric; Rating 62.5mW - ±1%; JLCPCB Part # C25744
R2, R6: 2k2; R_0402_1005Metric; Rating 62.5mW - ±1%; JLCPCB Part # C25879
R3: 4k7; R_0402_1005Metric; Rating 62.5mW - ±1%; JLCPCB Part # C25900
R4: 330R; R_0402_1005Metric; Rating 62.5mW - ±1%; JLCPCB Part # C25104
R7: 91k; R_0402_1005Metric; Rating 62.5mW - ±1%; JLCPCB Part # C4147
TP1, TP2, TP3: TestPoint_Small; TestPoint_Pad_D1.0mm
TP5: TestPoint; TestPoint_Pad_2.5x2.5mm
U1: AP3015KTR-G1; SOT-23-5; JLCPCB Part # C151334
U2: AP2210K-3.3TRG1; SOT-23-5; JLCPCB Part # C176959

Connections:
GND: C1.2, C3.2, C4.2, C5.2, C6.2, D2.5 (K), D3.2 (A), Q3.3 (G), Q4.1 (S), Q4.2 (S), Q4.3 (S), R4.2, R6.2, R8.2, TP1.1, U1.2 (GND), U2.2 (GND); also elsewhere on the board
GND1: D3.1 (K), GND1.1, Q4.5 (D)
unnamed: D1.2 (A), Q3.2 (S), R4.1
unnamed: D2.1 (A), D2.3 (A), R3.2
unnamed: D2.2 (A), D2.6 (K)
unnamed: D2.4 (K), Q2.2 (B1)
unnamed: D4.2 (A), L1.2, U1.1 (SW)
unnamed: Q1.1 (B), Q3.1 (D), R1.2
unnamed: Q2.5 (B2), Q2.6 (C1)
unnamed: Q2.4 (E2), Q4.4 (G), R2.2
unnamed: C2.2, R7.2, R8.1, U1.3 (FB)
SVIN: C1.1, R5.2, R6.1; also elsewhere on the board
VBUS: Q1.2 (E), Q2.1 (E1), Q2.3 (C2), R1.1, R5.1, TP5.1; also elsewhere on the board
VCC: C2.1, C3.1, C5.1, D4.1 (K), R2.1, R3.1, R7.1, TP2.1, U2.1 (VIN), U2.3 (EN); also elsewhere on the board
VDC: C4.1, D1.1 (K), L1.1, Q1.3 (C), U1.4 (~SHDN), U1.5 (IN)
VDD: C6.1, TP3.1, U2.5 (VOUT); also elsewhere on the board

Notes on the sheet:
3V366 ~ 3V234
9V~12V
1V2~18V
12V4

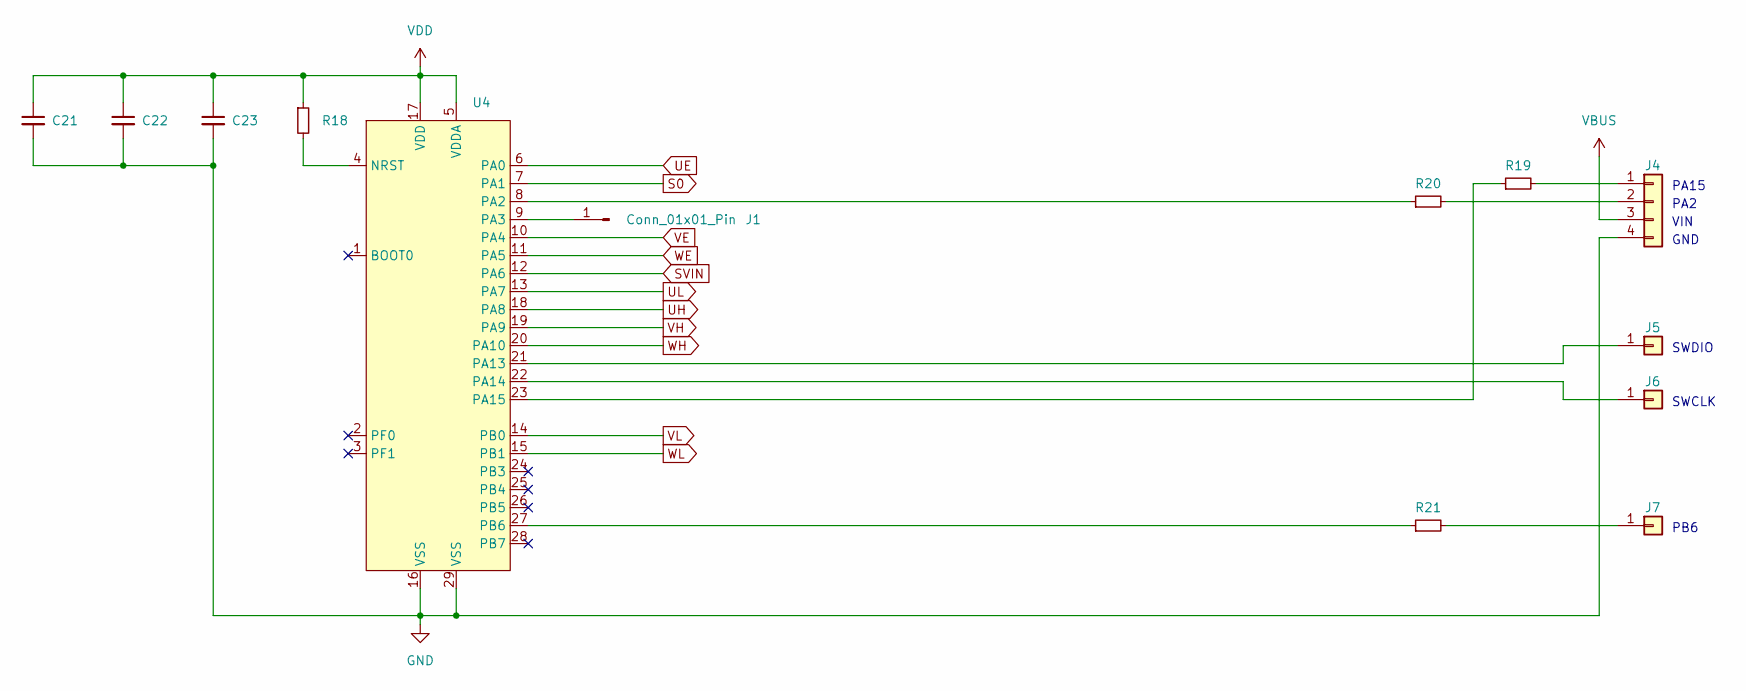
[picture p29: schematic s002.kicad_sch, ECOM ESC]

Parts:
C21: 10uF; C_0603_1608Metric; Rating X5R - 25V - ±20%; JLCPCB Part # C96446
C22, C23: 100nF; C_0402_1005Metric; Rating X7R - 16V - ±10%; JLCPCB Part # C1525
J1: Conn_01x01_Pin; Pad0.5
J4: Conn_01x04; HDG 1x04 P0.6 Horizontal; JLCPCB Part # C3008763
J5, J6, J7: Conn_01x01; TestPoint_Pad_1.0x1.0mm
R18: 10k; R_0402_1005Metric; Rating 62.5mW - ±1%; JLCPCB Part # C25744
R19, R20, R21: 1k; R_0402_1005Metric; Rating 62.5mW - ±1%; JLCPCB Part # C11702
U4: AT32F421G8U7; QFN-28-1EP_4x4mm_P0.4mm_EP2.6x2.6mm; JLCPCB Part # C2765098

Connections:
GND: C21.2, C22.2, C23.2, J4.4, U4.16 (VSS), U4.29 (VSS); also elsewhere on the board
unnamed: J1.1, U4.9 (PA3)
unnamed: J4.1, R19.2
unnamed: J4.2, R20.2
unnamed: J5.1, U4.21 (PA13)
unnamed: J6.1, U4.22 (PA14)
unnamed: J7.1, R21.2
unnamed: R18.2, U4.4 (NRST)
unnamed: R20.1, U4.8 (PA2)
unnamed: R19.1, U4.23 (PA15)
unnamed: R21.1, U4.27 (PB6)
S0: U4.7 (PA1); also elsewhere on the board
SVIN: U4.12 (PA6); also elsewhere on the board
UE: U4.6 (PA0); also elsewhere on the board
UH: U4.18 (PA8); also elsewhere on the board
UL: U4.13 (PA7); also elsewhere on the board
VBUS: J4.3; also elsewhere on the board
VDD: C21.1, C22.1, C23.1, R18.1, U4.5 (VDDA), U4.17 (VDD); also elsewhere on the board
VE: U4.10 (PA4); also elsewhere on the board
VH: U4.19 (PA9); also elsewhere on the board
VL: U4.14 (PB0); also elsewhere on the board
WE: U4.11 (PA5); also elsewhere on the board
WH: U4.20 (PA10); also elsewhere on the board
WL: U4.15 (PB1); also elsewhere on the board

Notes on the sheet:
VIN
PA15
SWCLK
PA2
GND
PB6
SWDIO

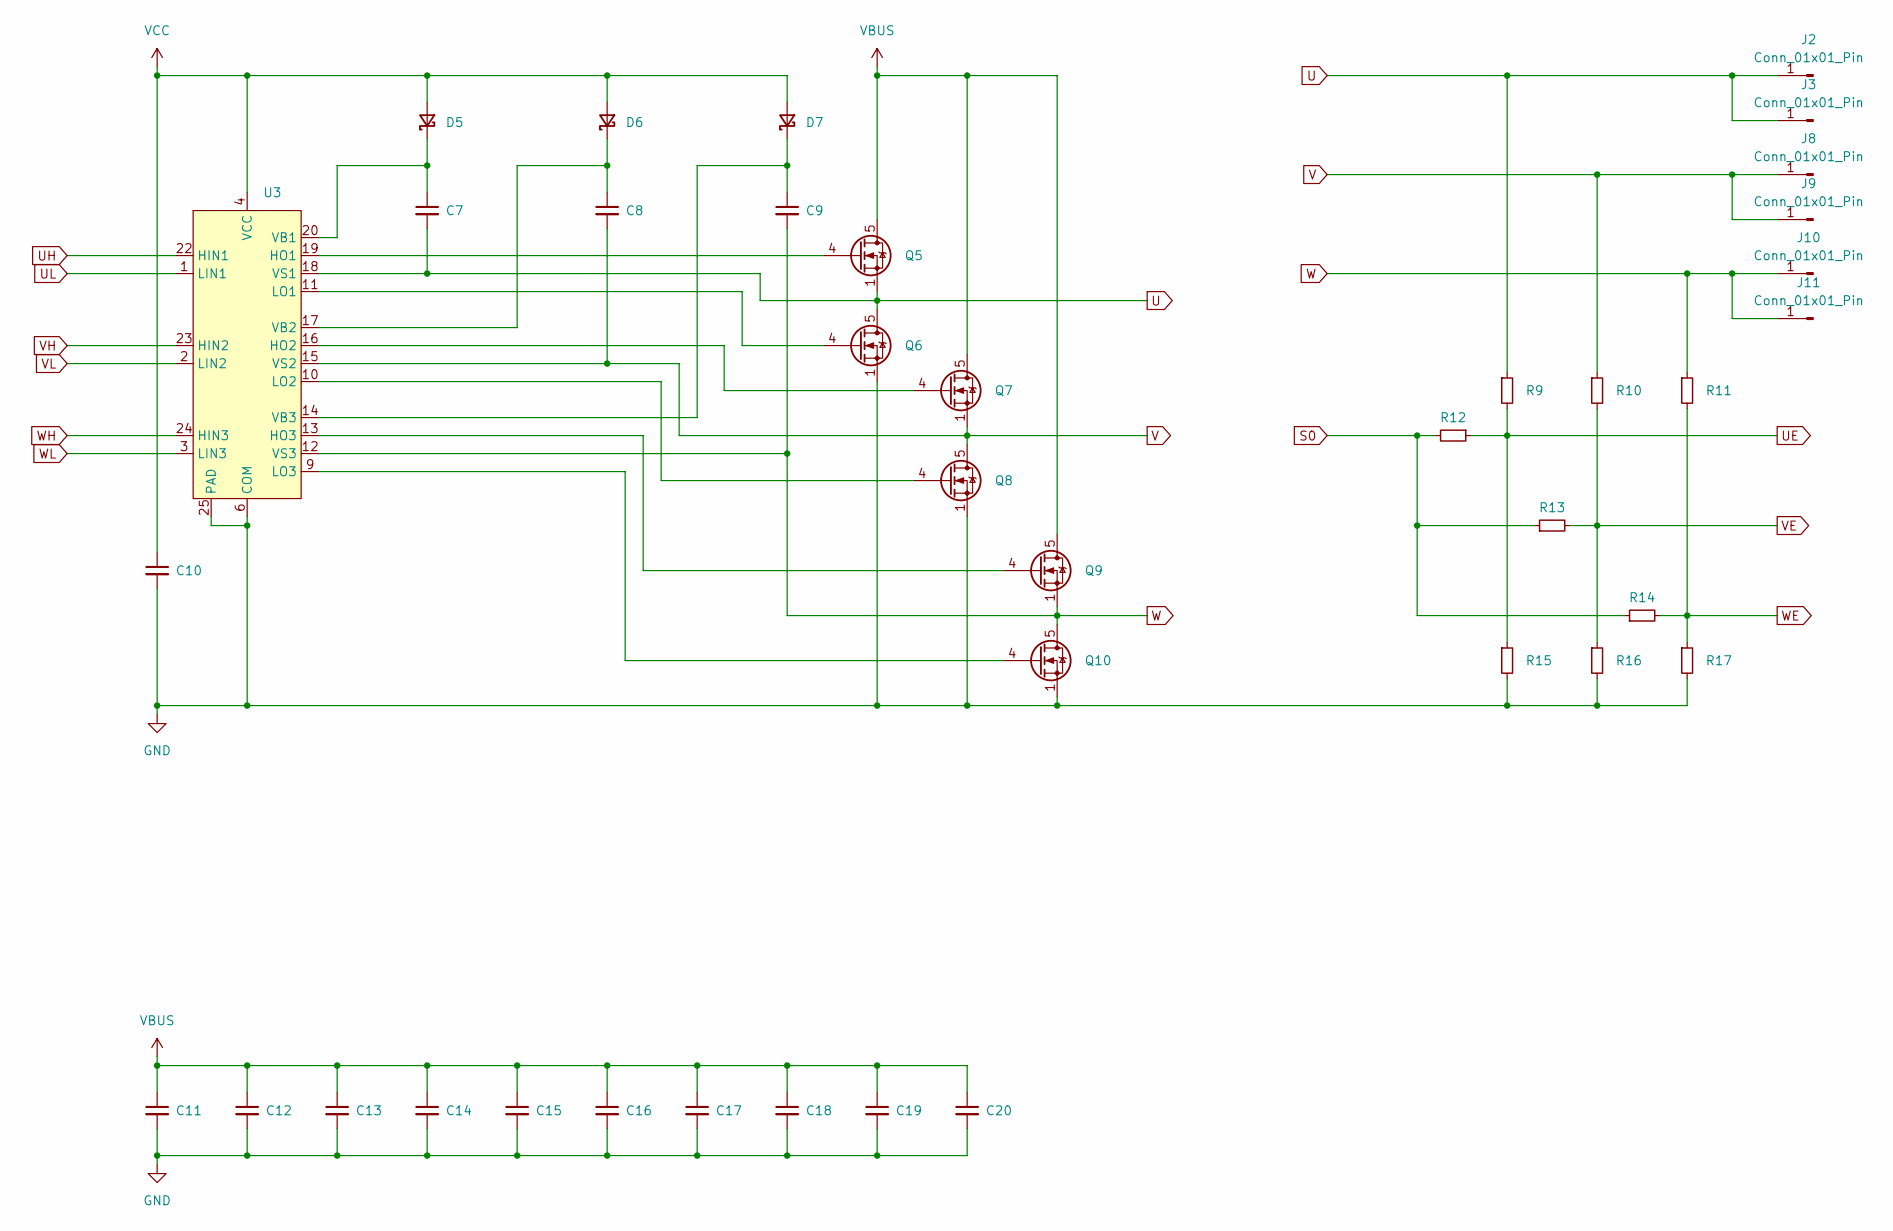
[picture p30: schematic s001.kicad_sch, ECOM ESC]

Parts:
C7, C8, C9: 220nF; C_0603_1608Metric; Rating X7R - 25V - ±10%; JLCPCB Part # C21120
C10: 1uF; C_0603_1608Metric; Rating X5R - 50V - ±10%; JLCPCB Part # C15849
C11, C12, C13: 22uF; C_0805_2012Metric; Rating X5R - 25V - ±20%; JLCPCB Part # C45783
C14, C15, C16, C17, C18, C19, C20: 22uF; C_0805_2012Metric_22µF; Rating X5R - 25V - ±20%; JLCPCB Part # C45783
D5, D6, D7: RB521SM-40T2R; D_SOD-523; JLCPCB Part # C253516
J2, J3, J8, J9, J10, J11: Conn_01x01_Pin; SolderWire-0.15sqmm_1x01_D0.5mm_OD1.5mm
Q5, Q6, Q7, Q8, Q9, Q10: JMSL0302AU; VSON-8_3.3x3.3mm_P0.65mm_NexFET; JLCPCB Part # C2890409
R9, R10, R11, R12, R13, R14: 10k; R_0402_1005Metric; Rating 62.5mW - ±1%; JLCPCB Part # C25744
R15, R16, R17: 2k2; R_0402_1005Metric; Rating 62.5mW - ±1%; JLCPCB Part # C25879
U3: FD6288Q; QFN-24-1EP_4x4mm_P0.5mm_EP2.6x2.6mm; JLCPCB Part # C328453

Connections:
GND: C10.2, C11.2, C12.2, C13.2, C14.2, C15.2, C16.2, C17.2, C18.2, C19.2, C20.2, Q6.1 (S), Q6.2 (S), Q6.3 (S), Q8.1 (S), Q8.2 (S), Q8.3 (S), Q10.1 (S), Q10.2 (S), Q10.3 (S), R15.2, R16.2, R17.2, U3.6 (COM), U3.25 (PAD); also elsewhere on the board
unnamed: C7.1, D5.1 (K), U3.20 (VB1)
unnamed: C8.1, D6.1 (K), U3.17 (VB2)
unnamed: C9.1, D7.1 (K), U3.14 (VB3)
unnamed: Q5.4 (G), U3.19 (HO1)
unnamed: Q6.4 (G), U3.11 (LO1)
unnamed: Q7.4 (G), U3.16 (HO2)
unnamed: Q8.4 (G), U3.10 (LO2)
unnamed: Q9.4 (G), U3.13 (HO3)
unnamed: Q10.4 (G), U3.9 (LO3)
S0: R12.2, R13.1, R14.1; also elsewhere on the board
U: C7.2, J2.1, J3.1, Q5.1 (S), Q5.2 (S), Q5.3 (S), Q6.5 (D), R9.1, U3.18 (VS1)
UE: R9.2, R12.1, R15.1; also elsewhere on the board
UH: U3.22 (HIN1); also elsewhere on the board
UL: U3.1 (LIN1); also elsewhere on the board
V: C8.2, J8.1, J9.1, Q7.1 (S), Q7.2 (S), Q7.3 (S), Q8.5 (D), R10.1, U3.15 (VS2)
VBUS: C11.1, C12.1, C13.1, C14.1, C15.1, C16.1, C17.1, C18.1, C19.1, C20.1, Q5.5 (D), Q7.5 (D), Q9.5 (D); also elsewhere on the board
VCC: C10.1, D5.2 (A), D6.2 (A), D7.2 (A), U3.4 (VCC); also elsewhere on the board
VE: R10.2, R13.2, R16.1; also elsewhere on the board
VH: U3.23 (HIN2); also elsewhere on the board
VL: U3.2 (LIN2); also elsewhere on the board
W: C9.2, J10.1, J11.1, Q9.1 (S), Q9.2 (S), Q9.3 (S), Q10.5 (D), R11.1, U3.12 (VS3)
WE: R11.2, R14.2, R17.1; also elsewhere on the board
WH: U3.24 (HIN3); also elsewhere on the board
WL: U3.3 (LIN3); also elsewhere on the board

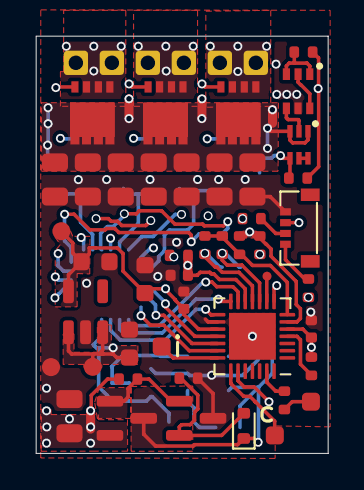
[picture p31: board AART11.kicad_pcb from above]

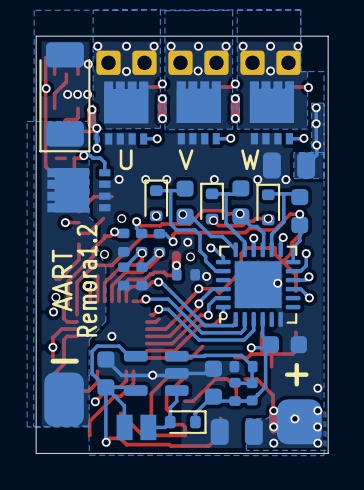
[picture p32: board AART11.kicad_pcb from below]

Board: 4 copper layers, 16.2 x 23.2 mm, 82 parts (31 on the bottom side), 48 nets.

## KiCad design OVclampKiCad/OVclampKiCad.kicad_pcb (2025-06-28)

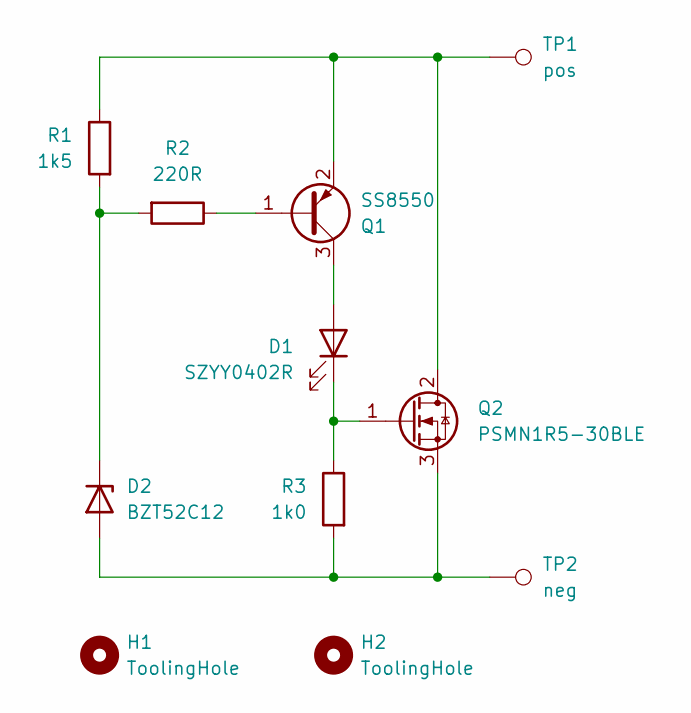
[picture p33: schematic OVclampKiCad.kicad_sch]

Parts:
D1: SZYY0402R; LED_0402_1005Metric_ReducedSilkScreen; JLCPCB Part # C434445
D2: BZT52C12; D_SOD-123F_ReducedSilkScreen; JLCPCB Part # C2891780
H1, H2: ToolingHole; ToolingHole_1.152mm
Q1: SS8550; SOT-23.kicad_NoSilkScreen_mod; JLCPCB Part # C8542
Q2: PSMN1R5-30BLE; TO-263-2.kicad_ReducedSilkscreen_mod; JLCPCB Part # C20755573
R1: 1k5; R_0402_1005Metric_NoSilkScreen; JLCPCB Part # C25867
R2: 220R; R_0402_1005Metric_NoSilkScreen; JLCPCB Part # C25091
R3: 1k0; R_0402_1005Metric_NoSilkScreen; JLCPCB Part # C11702
TP1: pos; SolderWirePad_1x01_SMD_5mmx5mm
TP2: neg; SolderWirePad_1x01_SMD_5mmx5mm

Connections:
unnamed: D1.2 (A), Q1.3 (C)
unnamed: D1.1 (K), Q2.1 (G), R3.1
unnamed: D2.2 (A), Q2.3 (S), R3.2, TP2.1
unnamed: D2.1 (K), R1.2, R2.2
unnamed: Q1.1 (B), R2.1
unnamed: Q1.2 (E), Q2.2 (D), R1.1, TP1.1

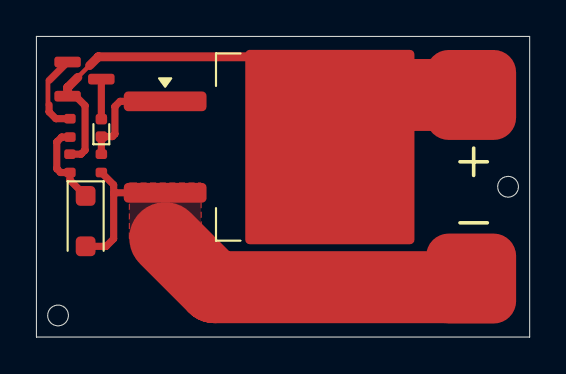
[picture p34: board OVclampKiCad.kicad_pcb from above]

Board: 2 copper layers, 27.4 x 16.7 mm, 11 parts (0 on the bottom side), 6 nets.

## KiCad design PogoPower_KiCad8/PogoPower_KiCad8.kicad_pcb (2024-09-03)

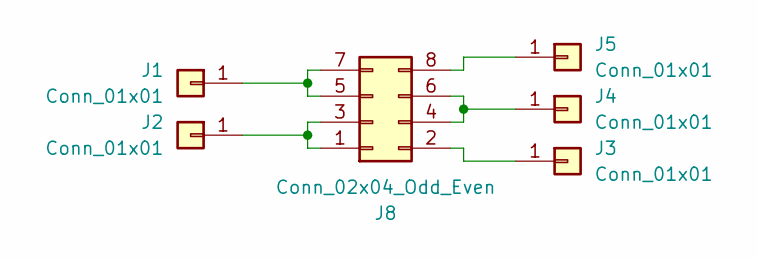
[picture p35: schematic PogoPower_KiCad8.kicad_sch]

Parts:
J1, J2, J3, J4, J5: Conn_01x01; PogoRecptacle_D1.4mm_OD2.0mm
J8: Conn_02x04_Odd_Even; PinHeader_2x04_P2.54mm_Vertical

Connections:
unnamed: J1.1, J8.5, J8.7
unnamed: J2.1, J8.1, J8.3
unnamed: J3.1, J8.2
unnamed: J4.1, J8.4, J8.6
unnamed: J5.1, J8.8

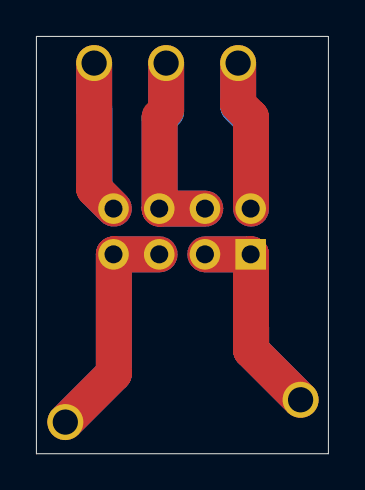
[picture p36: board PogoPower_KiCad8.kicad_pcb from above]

Board: 2 copper layers, 16.2 x 23.2 mm, 6 parts (1 on the bottom side), 5 nets.

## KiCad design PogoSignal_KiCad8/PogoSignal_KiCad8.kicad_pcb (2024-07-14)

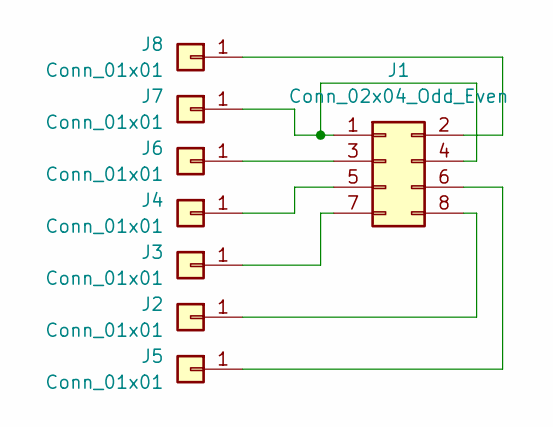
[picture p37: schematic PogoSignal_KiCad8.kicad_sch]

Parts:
J1: Conn_02x04_Odd_Even; PinHeader_2x04_P2.54mm_Vertical
J2, J3, J4, J5, J6, J7, J8: Conn_01x01; PogoRecptacle_D1.4mm_OD2.0mm

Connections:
unnamed: J1.1, J1.4, J7.1
unnamed: J1.2, J8.1
unnamed: J1.3, J6.1
unnamed: J1.5, J4.1
unnamed: J1.6, J5.1
unnamed: J1.7, J3.1
unnamed: J1.8, J2.1

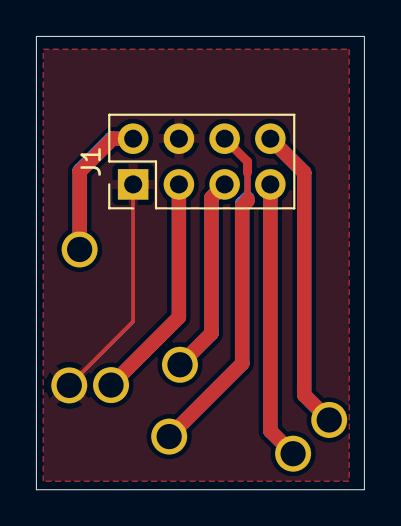
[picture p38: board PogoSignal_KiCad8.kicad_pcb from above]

Board: 2 copper layers, 18.2 x 25.2 mm, 8 parts (0 on the bottom side), 7 nets.

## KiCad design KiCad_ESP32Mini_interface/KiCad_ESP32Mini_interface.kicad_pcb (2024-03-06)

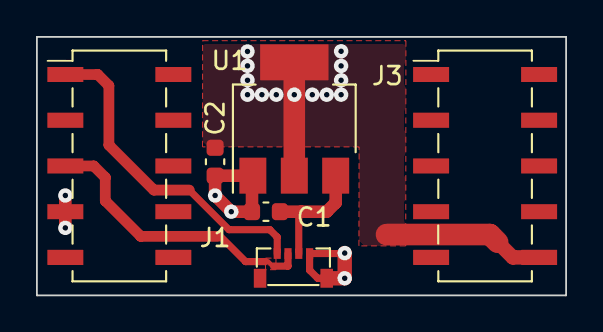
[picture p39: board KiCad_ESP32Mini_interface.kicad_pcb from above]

Board: 2 copper layers, 29.4 x 14.4 mm, 6 parts (0 on the bottom side), 5 nets.

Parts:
C1, C2: 1µF 50V; C_0603_1608Metric
J1, J3: Conn_02x05_Odd_Even; C843271_PinSocket_2x05_P2.54mm_Vertical_SMD_OddEven
J2: Conn_01x04; HDG 1x04 P0.6 Horizontal
U1: LDL1117S33R_SOT223; SOT-223-3_TabPin2

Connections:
unnamed: J1.1, J2.1
unnamed: J1.5, J2.2
unnamed: C1.2, C2.2, J1.7, J2.4, U1.1 (GND)
unnamed: C1.1, J2.3, U1.3 (VI)
unnamed: C2.1, J3.10, U1.2 (VO)

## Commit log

2023-12-21 Added requirements doc
    [slot-car-ecom-requirements.ods]
2024-03-06 Added mini if
    [KiCad_ESP32Mini_interface.kicad_pcb, KiCad_ESP32Mini_interface.kicad_sch, bom.csv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]
2024-03-23 Updated binaries w 100% pwm
2024-04-07 Updated v8 fix footprints
    [AART11.kicad_pcb, AART11.kicad_sch, bom.csv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]
2024-04-07 Added inductor fp
    [AART11.kicad_pcb, AART11.kicad_sch, bom.csv]
2024-04-15 Update KiCad fix L1
2024-04-19 Added ss
    [SettingsAndDragBrake.ods]
2024-04-23 Get KiCad right V7
    [AART11.kicad_pcb, AART11.kicad_sch, bom.csv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]
2024-04-23 Added wifi encl
    [WiFi_Box.stl, WiFi_Lid.stl]
2024-04-23 Get bom and posn right
    [bom.csv, positions.csv]
2024-05-15 Added pkg
    [MidA.kicad_pcb, MidA.kicad_sch, bom.csv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]
2024-07-14 Added flashing boards
    [PogoPower_KiCad8.kicad_pcb, PogoPower_KiCad8.kicad_sch, PogoSignal_KiCad8.kicad_pcb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]
2024-09-03 Pogo Power slikscreen
    [PogoPower_KiCad8.kicad_pcb, PogoPower_KiCad8.kicad_sch, bom.csv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]
2024-09-11 Better fets
    [AART11.kicad_pcb, AART11.kicad_sch, bom.csv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]
2024-09-16 Added CAD for board carrier
    [CradleReverse1.stl]
2024-09-27 Staged binaries for test
2024-11-02 Wrong part number
    [AART11.kicad_pcb, AART11.kicad_sch, bom.csv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]
2024-12-05 Gerber for the jig
    [bom.csv, designators.csv, positions.csv]
2025-05-26 Added clamp doc
2025-05-26 Updated requirements, added lid
    [WiFi_Lid2.stl, slot-car-ecom-requirements.ods]
2025-06-28 Added clamp
    [AART11.step, OVclampKiCad.kicad_pcb, OVclampKiCad.kicad_sch]
2025-06-30 KiCad 9 update
    [AART11.kicad_pcb, AART11.kicad_sch, s001.kicad_sch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]
2025-08-11 A better box
    [WiFiBox2.stl, WiFi_Box.stl, WiFi_Lid.stl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]
2026-03-19 High pwm freq binaries for high Kv motors
